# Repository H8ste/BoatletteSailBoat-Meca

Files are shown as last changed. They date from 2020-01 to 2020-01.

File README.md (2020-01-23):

# BoatletteSailBoat-Meca
Repository for the mechanical aspects of the sailboat project created by Medialogy Msc students from Aalborg University. 
Link to the other repositories: [Arduino Repository](https://github.com/H8ste/SailBoatArduinoInterface) & [ROS Repository](https://github.com/H8ste/SailBoatROS) & [Visualisation Repository](https://github.com/H8ste/Boatplatform-visualisation).

## Hardware used in the project
The hardware used in the project can be seen in the table below. 

| Hardware list | |
|:---:|---|
| Microcontroller (Brain) | Raspberry Pi 4 Model B 4 GB |
| SD card | SanDisk MicroSD card 16gb |
| Microcontroller (Slave) | Arduino Mega 2560 R3 with ATmega16U2 serial chip |
| Extension board | Grove - Mega Shield v1.2 |
| Servo Shield | Adafruit 16-Channel 12-bit PWM/ServoShield - I2C interface |
| Servos | Winch servo and Standard 180 degree servo |
| Wind vane | AEAT-6010 magnetic encoder with custom 3D-printed vane |
| GPS | Adafruit Ultimate GPS Breakout v3 |
| IMU | Adafruit BNO055 |
| Step-Up/Step-Down VoltageRegulator | Polulu Step-Up/Step-Down Voltage Regulator S7V8A |
| Transmitter | FrSky Taranis Q X7 |
| Receiver | FrSky X4R 4ch 2.4Ghz ACCST Receiver |

A BOM (Bill Of Materials) is available in the [Electronics info folder](https://github.com/H8ste/BoatletteSailBoat-Meca/tree/master/Electronics%20info). 

## 3D Prints 
All the STL files for 3D printing the different parts are available in the [3D Prints folder](https://github.com/H8ste/BoatletteSailBoat-Meca/tree/master/3D%20Prints). The printer used for printing was an **Ultimaker 2 Extended**. The defeault settings for most of the prints were: **20% Grid Infill , Support ON, 50° Overhang Angle, Plastic: PLA, 0.4 mm Nozzle**.

### Source 3D Projects for all printed parts
The 3D models were created in Tinkercad. If you want to modify the models to fit your project, the projects are available here: [Wind Vane](https://www.tinkercad.com/things/89tcWYWsKEA), [Wind Vane Mount](https://www.tinkercad.com/things/2fnjmZwuIq8), [Hatch](https://www.tinkercad.com/things/8WWAtZOIEZg), [Screwpress for Hatch](https://www.tinkercad.com/things/6mcEZHj0BVj), [Arduino & Pi Box](https://www.tinkercad.com/things/kBA1OZy1NIk), [IMU & GPS Box](https://www.tinkercad.com/things/99QlRKgLktw).

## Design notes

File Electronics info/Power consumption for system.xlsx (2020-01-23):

 | Power Consumption
Component | Volt(V) | Current(mA) | Power(mW) |  |  | Arduino Power Limits |  | Raspberry Pi Power Limits
GPS | 5 | 20 | 100 |  |  | Max per pin | 40 mA | Recommended PSU current capacity | 3.0 A
IMU | 3.6 | 27.7 | 100 |  |  | Recommended max per pin | 20 mA | Maximum total USB peripheral current draw | 1.2 A
Vind vane | 5 | 22 | 120 |  |  | Max VDD or GND current | 200 mA | Typical bare-board active current consumption | 600 mA
Arduino | 5 | 70 | 350 |  |  | Max operating voltage | 6 V | Max operating voltage | 5.25 V
Total Arduino |  | 139.7 | 670 |  |  | Source (from datasheet) (https://i.stack.imgur.com/FAovO.png) |  | Source (https://www.raspberrypi.org/documentation/faqs/)
Raspberry Pi | 5 | 600 | 3000
Total System |  | 739.7 | 3670
 | Battery math
Power supply |  |  | 41580 | mWh
 |  |  | 11.33 | hours | However a battery stops before it is out of mW to sustain the ability to recharge.
 |  |  | 4.9hours with new battery

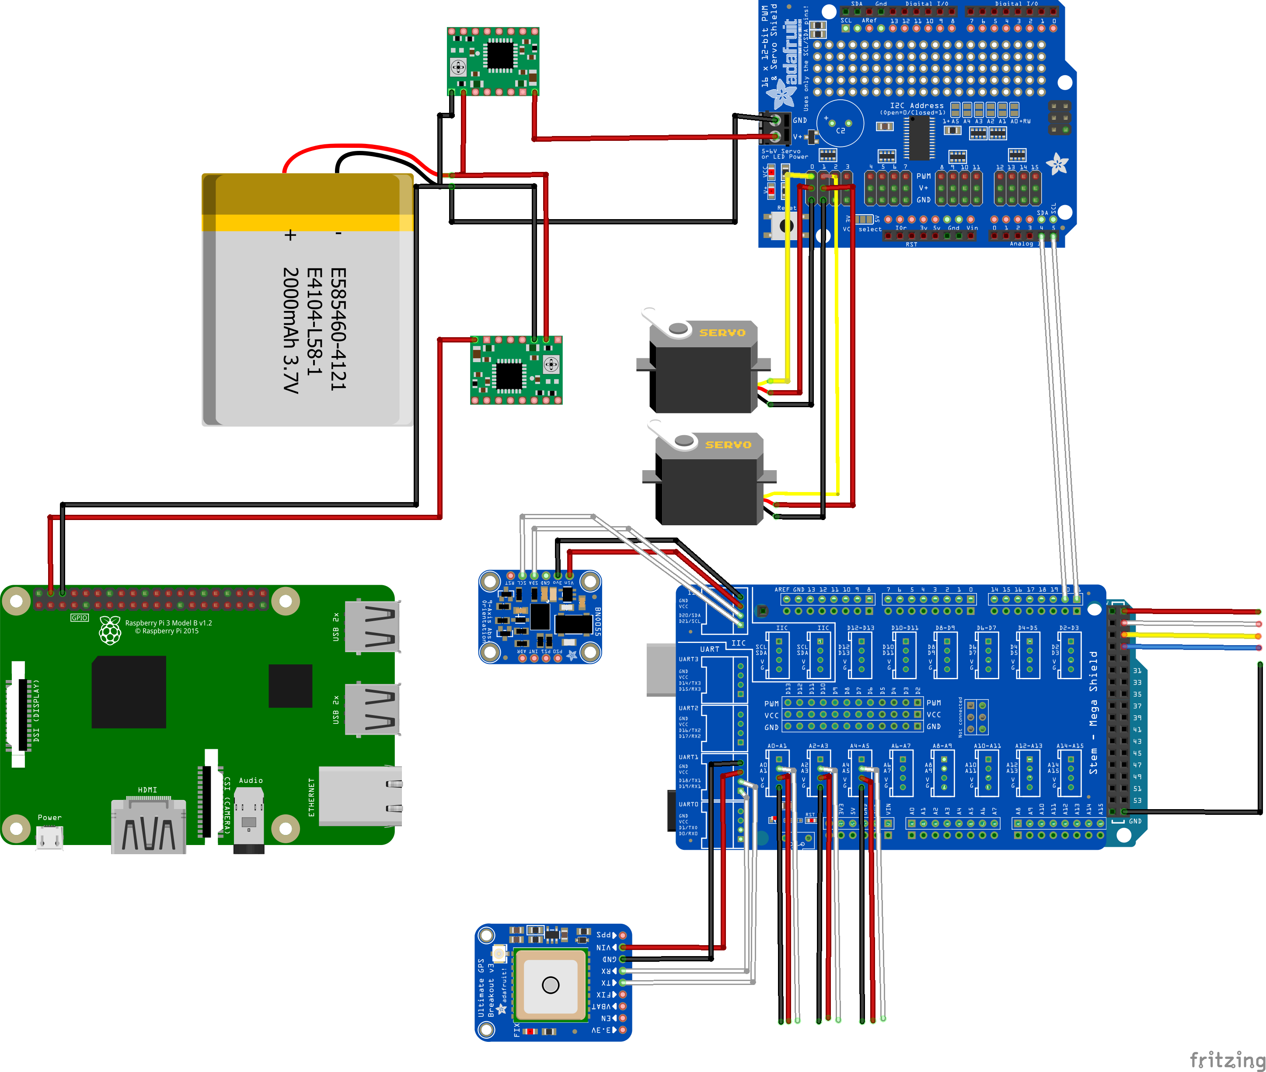
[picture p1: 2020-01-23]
Electronics info/Boatlette_Schematic.png

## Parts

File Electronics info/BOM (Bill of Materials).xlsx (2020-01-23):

Components | Reference | Link to product | Price | Notes | Estimated Weight (in grams)
Adafruit Ultimate GPS Breakout - 66 channel w/10 Hz updates - Version 3 Sensor | Recommended by Vautier et al. | https://www.adafruit.com/product/746 | 270.65 kr. |  | 10
Grove - Mega Shield v1.2 | Recommended by Vautier et al. | https://www.seeedstudio.com/Grove-Mega-Shield-v1-2-p-2539.html | 67.00 kr. | With the shield the Arduino can connect the different sensors with pin sockets, which will greatly reduce the possibility of deataching from the pin. | 58
3D Printed Wind Vane (Rotary encoder, bearings, nuts and bolts & PLA plastic for printing) |  | https://www.digikey.com/catalog/en/partgroup/aeat-6010-6012-magnetic-encoder/11831 | 180.00 kr. | Estimated prices; rotary encoder 100 DKK, plastic 20 DKK, bearings 40 DKK, nuts and bolts 20 DKK | 140
Adafruit 16-Channel 12-bit PWM/Servo Shield - I2C interface | Recommended by Vautier et al. | https://www.adafruit.com/product/1411 | 118.49 kr. | The servo creates signal noise if not localized by a shield. | 71
Arduino Mega 2560 R3 with ATmega16U2 serial chip | Recommended by Vautier et al. | https://www.sparkfun.com/products/11061 | 107.00 kr. | Arduino Mega has more digital and analog pins, better processor and flash memory compared to Arduino Uno. | 37
Raspberry Pi 4 Model B | Recommended by Vautier et al. | https://thepihut.com/products/raspberry-pi-4-model-b | 465.00 kr. | Raspberry PI 3 is used in the tutorial but Raspberry PI 4 could be utilized to increase the computational power of the system. However, the Raspberry Pi 4 draws more power. | 42
Connectors, wires, pin head connectors, soldering material etc. |  |  | 100.00 kr. | Price depends on availability of tools and materials
IMU -BNO055 |  | https://www.digikey.com/product-detail/en/bosch-sensortec/BNO055/828-1058-1-ND/6136309 | 75.00 kr. |  | 80
Power supply (Zippy Compact 1800mAh 2S 6.6V 30C 60C LiFePo) |  | https://www.ebay.com/itm/Zippy-Compact-1800mAh-2S-6-6V-30C-60C-LiFePo-Battery-Pack-XT60-Multirotor-Car/153651437366 | 117.00 kr. |  | 400
SD card for the Raspberry |  | https://shop.pimoroni.com/products/noobs-32gb-microsd-card-3-1 | 119.00 kr. |  | 0.8
2X Pololu Adjustable Step-Up/Step-Down Voltage Regulator S7V8A |  | https://www.pololu.com/product/2118 | 160.00 kr. |  | 0.6
Transmitter (FrSky Taranis Q X7) |  | https://hobbyking.com/en_us/frsky-taranis-q-x7-int-l-version-digital-telemetry-radio-system-2-4ghz-accst-black-no-plugs.html | 702.00 kr. |  | 5.8
Receiver (FrSky X4R 4ch 2.4Ghz ACCST Receiver) |  | https://www.ercmarket.com/frsky-x4r-4ch-2.4ghz-accst-receiver-w-telemetrie-frs-x4r.html | 270.00 kr.
Total |  | Total price: | 2751.14 kr. | Minimum total weight: | 845.2
 |  | In Euro: | €368.13

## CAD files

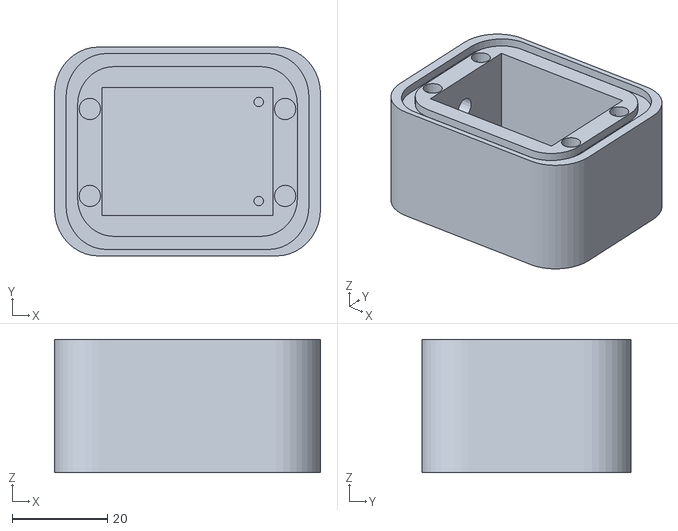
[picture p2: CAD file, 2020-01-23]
3D Prints/GPS and IMU box/gps/gps_box.stl
56.0 x 44.0 x 28.0

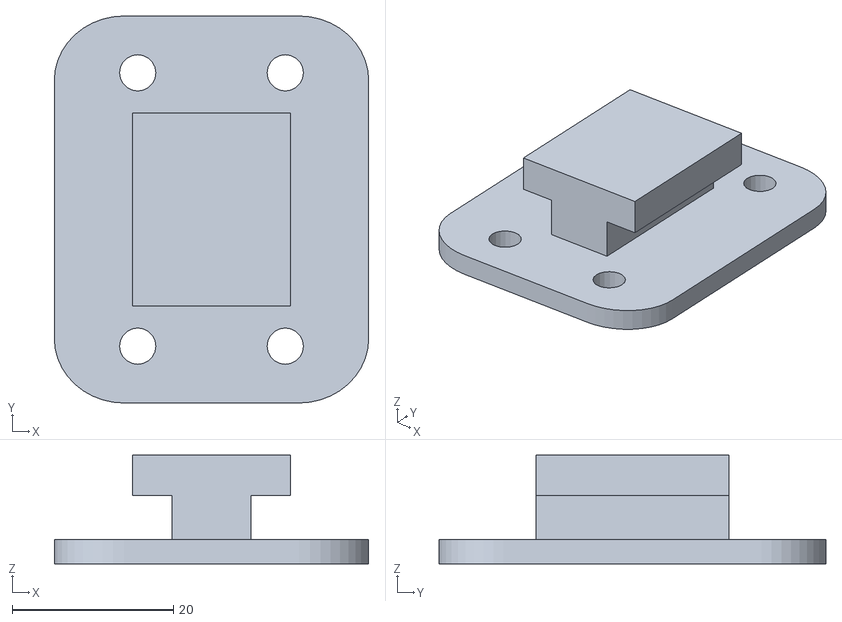
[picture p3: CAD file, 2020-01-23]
3D Prints/GPS and IMU box/imu/imu_top.stl
39.0 x 48.0 x 13.5

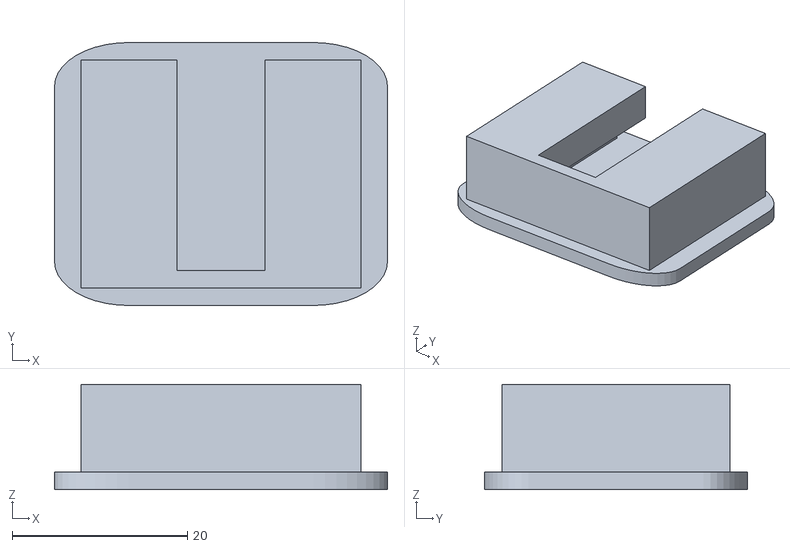
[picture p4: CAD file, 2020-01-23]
3D Prints/GPS and IMU box/mount2.stl
38.0 x 30.0 x 12.0

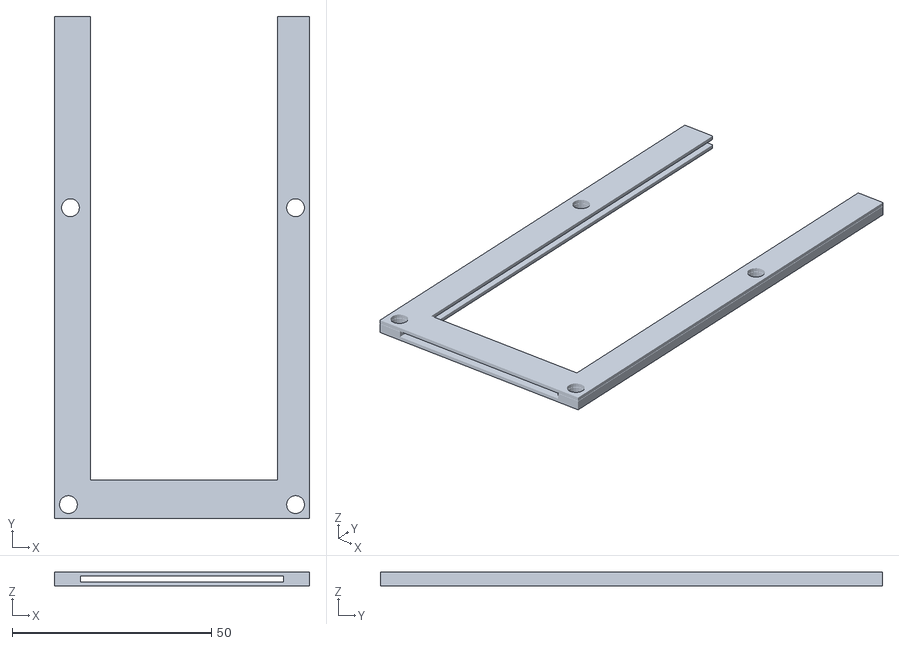
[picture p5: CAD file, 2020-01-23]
3D Prints/Hardware Box/mega _ pi top1.stl
64.0 x 126.0 x 3.60

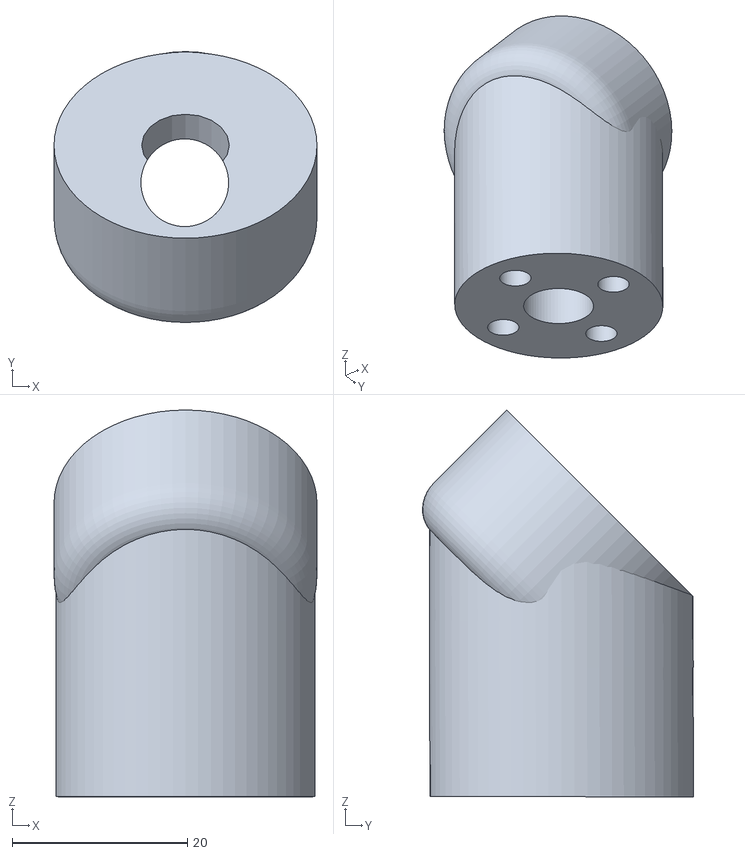
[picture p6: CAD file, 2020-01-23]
3D Prints/Wind Sensor/Mount/sensor_arm_top.stl
30.0 x 30.9 x 44.2

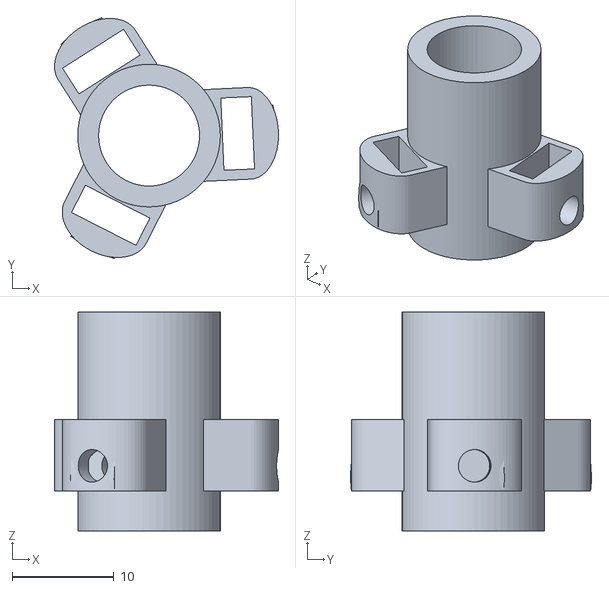
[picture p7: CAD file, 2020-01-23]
3D Prints/Wind Sensor/Vane and casing/BearingHolder.stl
22.0 x 23.6 x 21.5

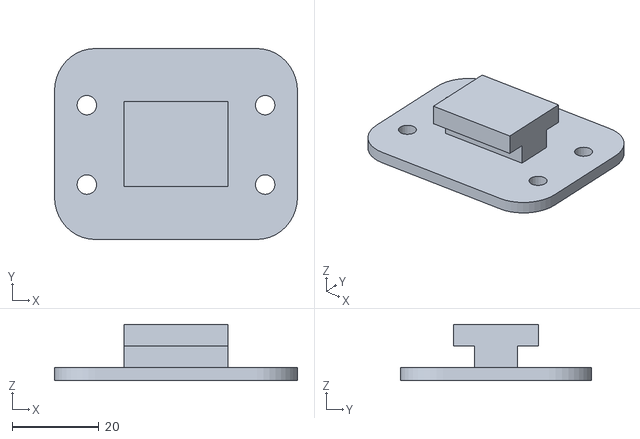
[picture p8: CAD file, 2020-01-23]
3D Prints/GPS and IMU box/gps/gps_top.stl
56.0 x 44.0 x 13.0

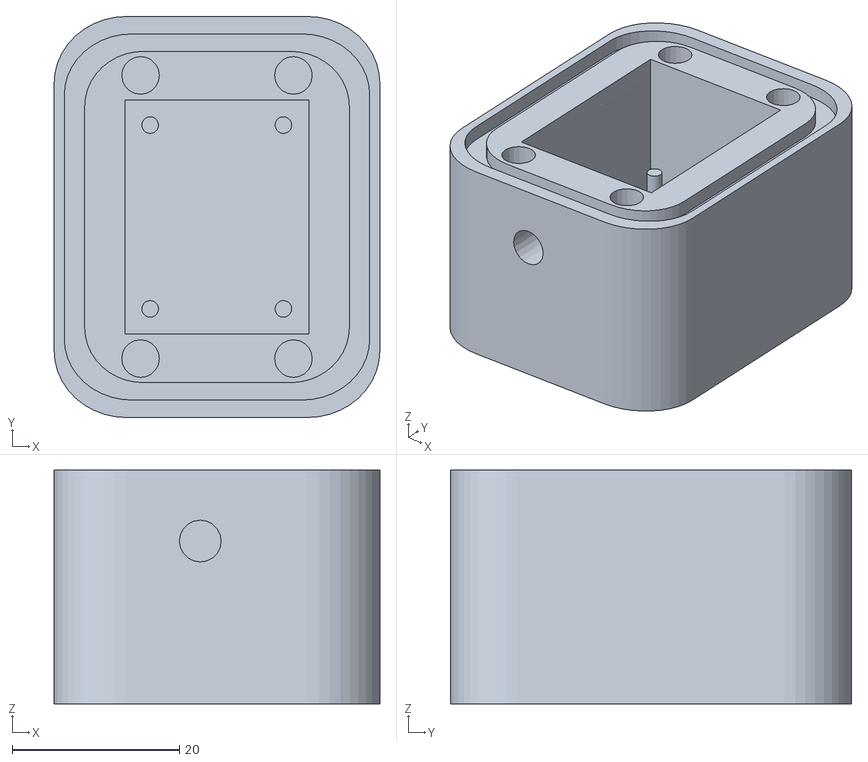
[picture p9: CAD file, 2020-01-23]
3D Prints/GPS and IMU box/imu/imu_box.stl
39.0 x 48.0 x 28.0

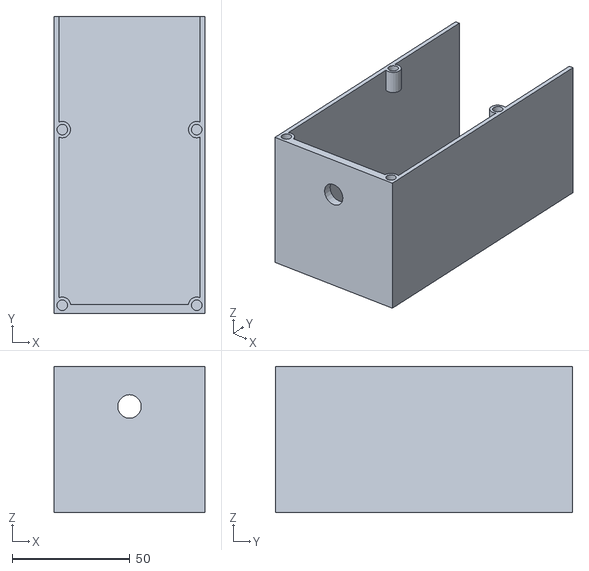
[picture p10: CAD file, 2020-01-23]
3D Prints/Hardware Box/mega _ pi box2.stl
64.0 x 126.0 x 62.0

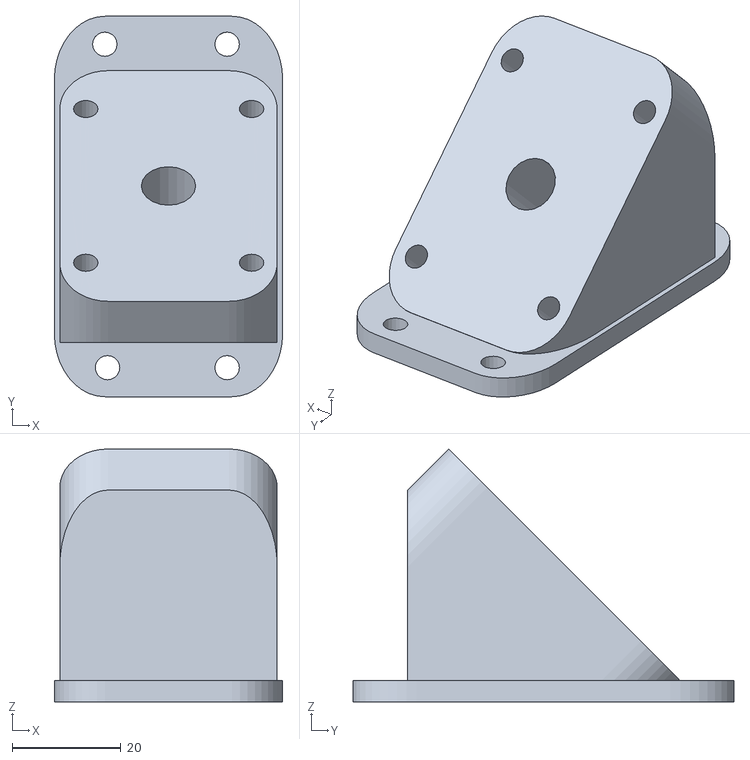
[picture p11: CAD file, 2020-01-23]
3D Prints/Wind Sensor/Mount/sensor_arm_socket.stl
42.0 x 70.0 x 46.5

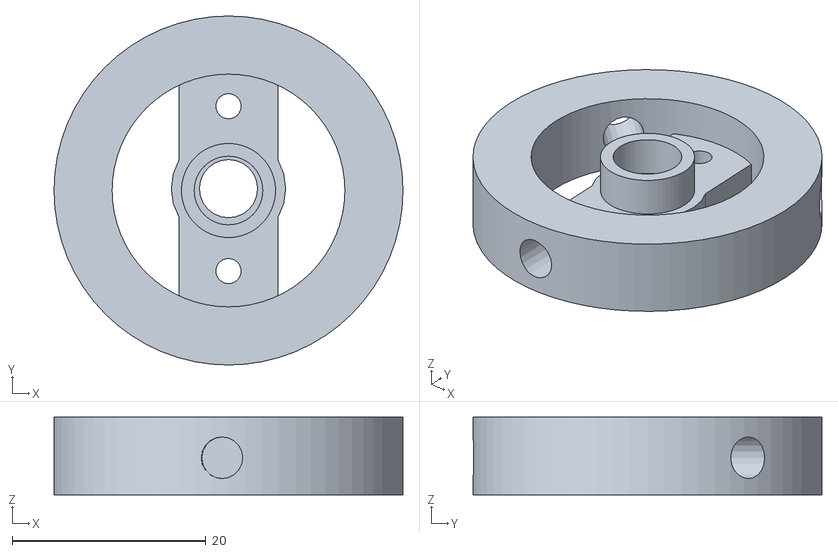
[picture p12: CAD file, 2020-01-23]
3D Prints/Wind Sensor/Vane and casing/REncoderHolder.stl
36.0 x 36.0 x 8.00

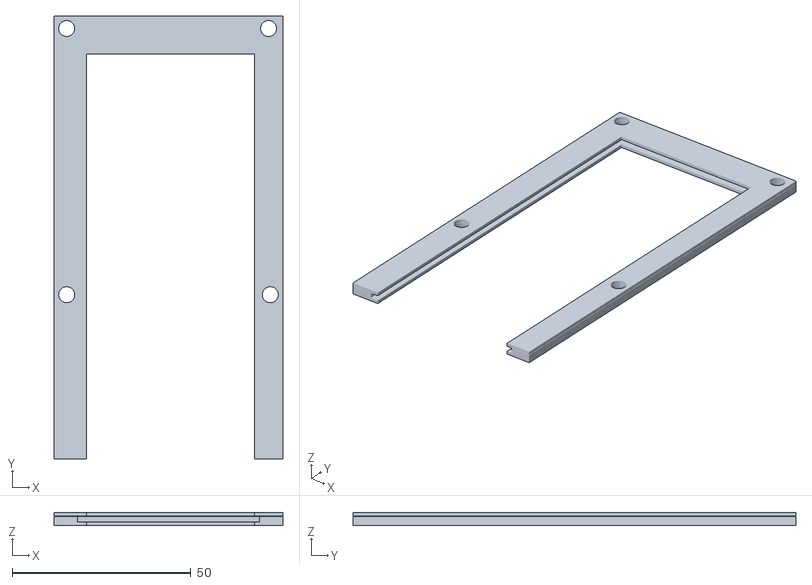
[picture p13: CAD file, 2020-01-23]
3D Prints/Hardware Box/mega + pi top2.stl
64.0 x 124.0 x 3.60

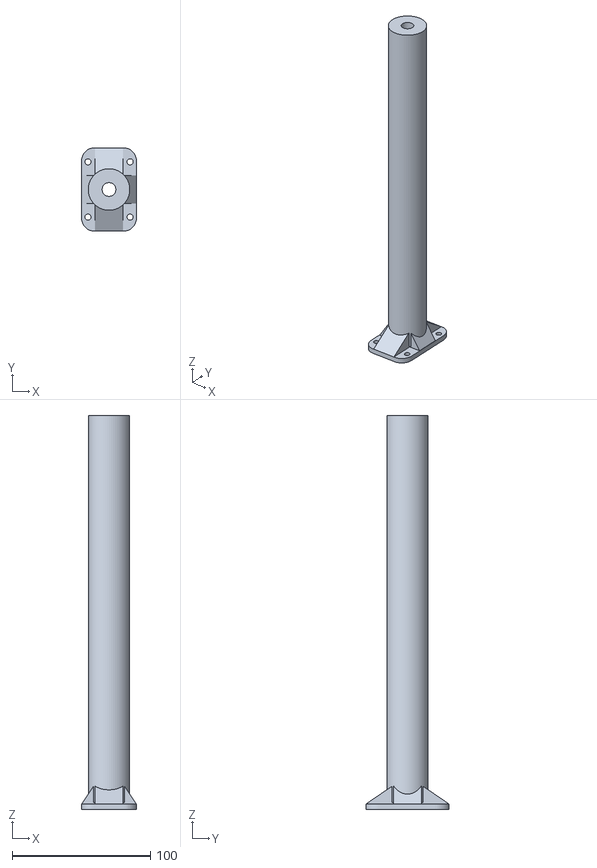
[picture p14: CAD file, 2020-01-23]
3D Prints/Wind Sensor/Mount/sensor_arm.stl
40.0 x 60.0 x 285.0

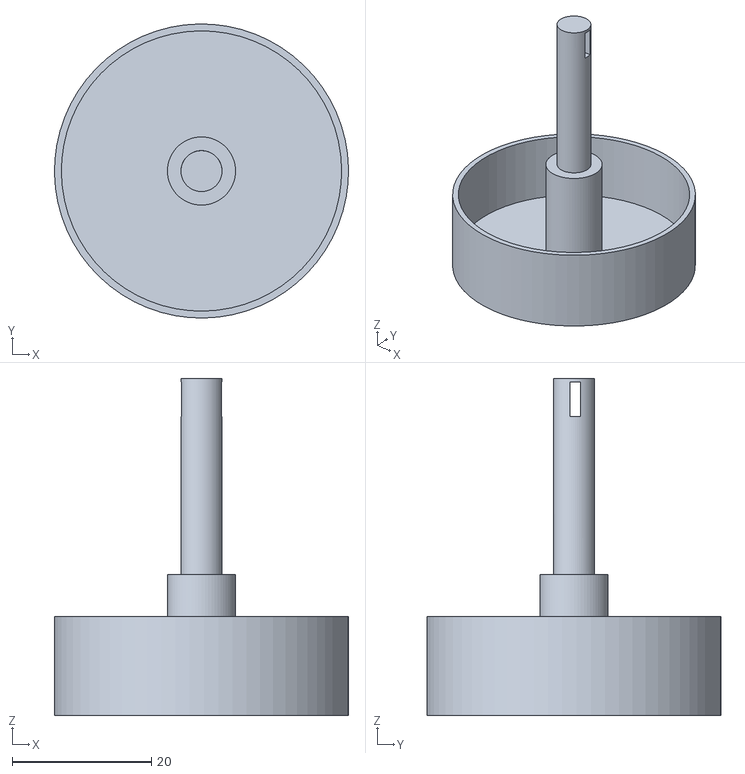
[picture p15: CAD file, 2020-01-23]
3D Prints/Wind Sensor/Vane and casing/VaneTop.stl
42.3 x 42.3 x 48.5

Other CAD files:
3D Prints/Hardware Box/mega _ pi box1.stl
3D Prints/Wind Sensor/Mount/sensor_arm_bottom_bottom.stl
3D Prints/Wind Sensor/Vane and casing/WindVanePointer.stl
3D Prints/Wind Sensor/Vane and casing/WindVanePointerTip.sts.stl
3D Prints/Hatch and Screwpress/hatch.stl
3D Prints/Hatch and Screwpress/hatch_ledge.stl
3D Prints/Hatch and Screwpress/screw press_w_boxholder.stl
3D Prints/Hatch and Screwpress/screw_press_104cm.stl
3D Prints/Hatch and Screwpress/screw_press_82cm.stl
3D Prints/Hatch and Screwpress/screw_press_90cm.stl
3D Prints/Hatch and Screwpress/screw_press_holders.stl
3D Prints/Wind Sensor/Vane and casing/ProtectiveRing.stl
3D Prints/Wind Sensor/Vane and casing/SupportHolder.stl
3D Prints/Wind Sensor/Vane and casing/VaneHull.stl

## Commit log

2020-01-23 Uploaded all STL files
    [BearingHolder.stl, ProtectiveRing.stl, REncoderHolder.stl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]
2020-01-23 Added schematic, bom, power and weight details
